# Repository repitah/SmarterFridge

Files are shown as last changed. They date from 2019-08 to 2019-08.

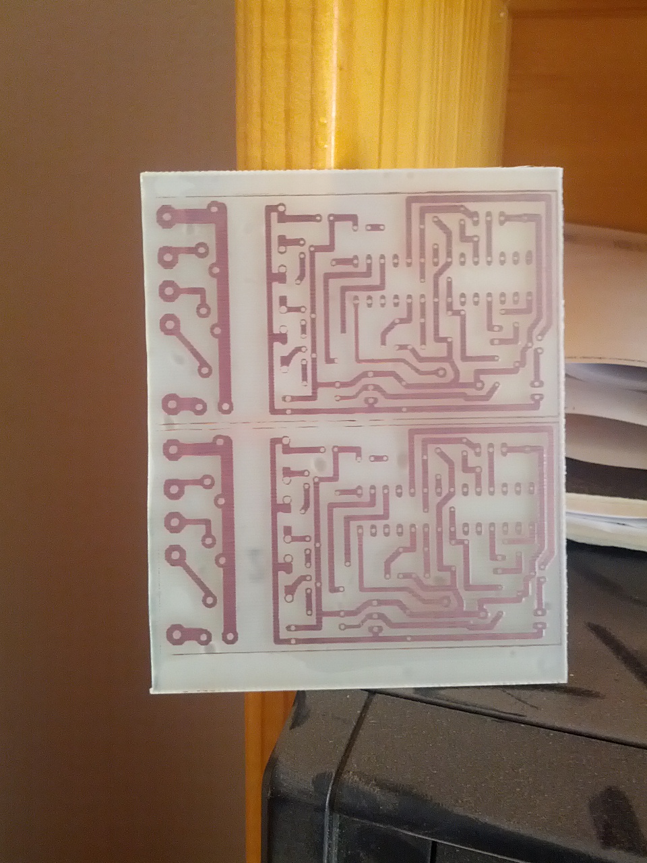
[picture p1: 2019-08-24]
Tests_misc/IMG_20130628_082345.jpg

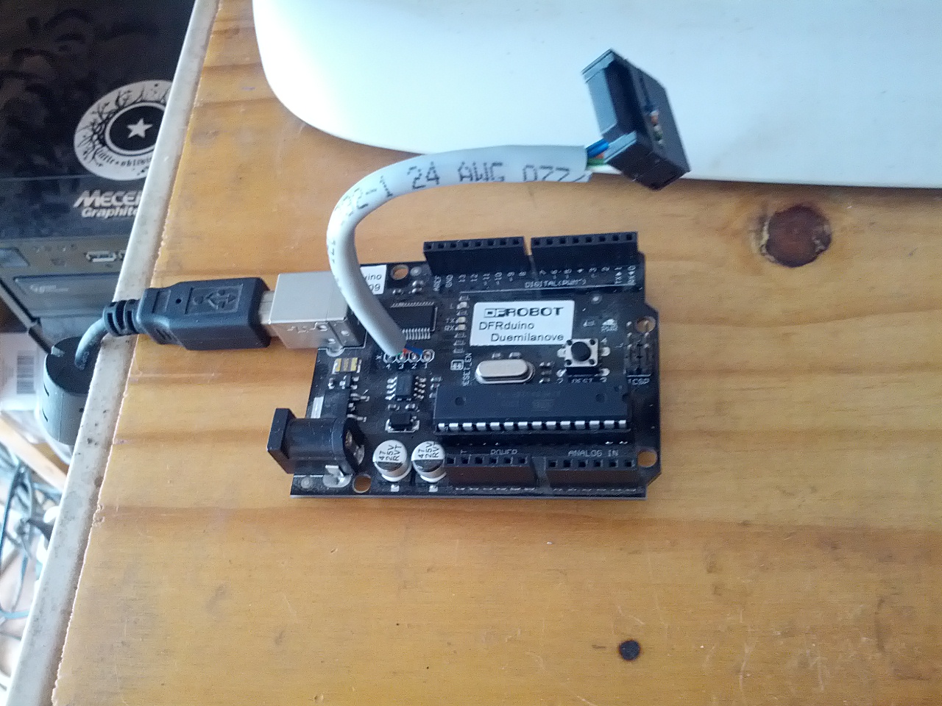
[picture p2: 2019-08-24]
Tests_misc/IMG_20130721_124718.jpg

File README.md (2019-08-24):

# SmarterFridge
Digital (AVR MCU) replacement for fridge analogue thermistat.
Circuit is essentially a custom Arduino with ATMEGA328P.

This is one of my first "major" projects (circa 2012), and a lot has been learnt since then.

Additional features (because why not)
* Fan to circulate air over the cooling radiator
  * Does not run the fan when the door is open
  * Gives an old and basic fridge more modern and expensive features.
* Door open/ajar reminder (buzzer)
* Anti-freeze / defroster (since the old fridge was a "frost-free" type.
* Does not start the compressor until the door is closed

Project notes:
* Circuit and PCB done with EagleCAD -- Only learnt basic KiCAD in a later project.
* Done with Code::Blocks (painful setup, but I wanted a half decent IDE. It should convert back to Arduno IDE fairly easily.
* In hindsight:
  * Software: not using the default Arduino bootloader may be better (doesn't pulse the pins on boot); (OptiBoot?)
  * Hardware: drive the transistors, from the MCU, via a resistor and have a pulldown
  * Hardware: There are nice modular 110V/220V mains to 12V modules that could shrink the total install package size.
  * Hardware: add simple debounce circuit to door switch. Maybe even a gated debounce.
  * Hardware: The fan turned out to be annoying in terms of humming sound. With a differnt type of fan and a custom 3D printed baffle, the idea could be promissing.
  * Hardware: Maybe port to a more modern cheap platform (ESP8266/ESP32) and/or surface mount components

Background story:
The fridge I got when I moved in to my first apartment was an old 80's/90's model that had been working reasonably well for the 5 years before this project was dreamed up. The driving reasons for this projects was: the replacement analogue thermistat was expensive; I had an interest in electronics for most of my life and had a dangerously primative knowledge of circuit (inspite of doing a few subjects in university); Arduinos were all the rage; I wanted to learn and most of the fancy fridges had some MCU type setup. Above all, the over-running of the compressor was costing me a small fortune in electricity and spoiling my fresh fruit and veg... it had to be fixed... I wanted to learn... I wasn't spending a small fortunate buying a new fridge because of 1 bad part.

My then partner, being a freshly minted professional programmer, helped me setup Code::Blocks as I wanted an IDE more akin to Visual Studio, or at least better than the basic notepad like setup that shipped for the Arduino back then (early 2010's).

The project was fun, learning about NTC resistors, voltage dividers, and even how to do lithography and make a PCB with cheap pool acid. It was also an introduction to HVAC to me -- something useful later in my career.

Sadly, 4 years later, I got home one warm summer evening and found the fridge had given up on me (I suspect a refridgerant leak, causing overheat/failure of the compressor) and was replaced with another basic fridge with analogue thermistat, the very next day -- and so this project may still be useful to necro at some point.

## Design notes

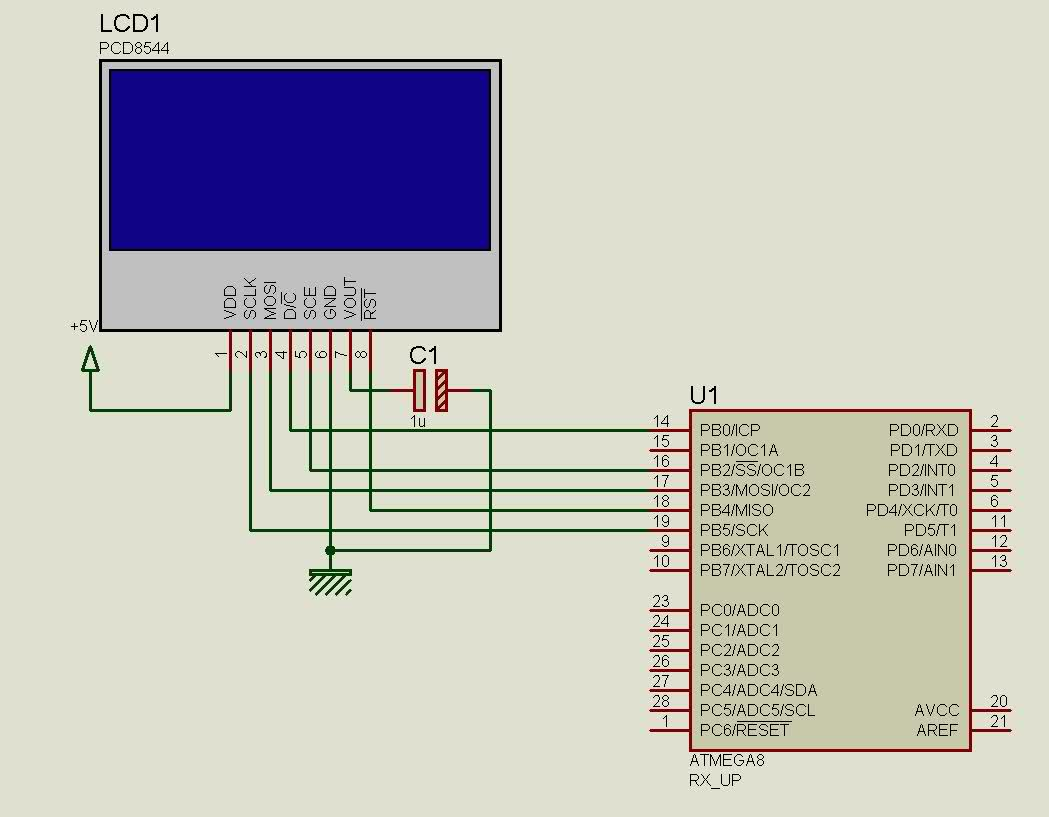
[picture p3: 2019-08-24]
Software/PCD8544/7ze9rr6f.bmp

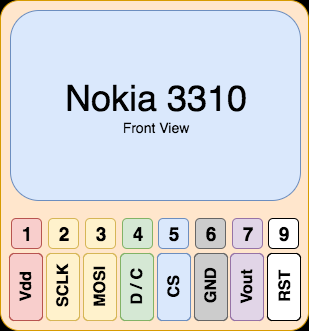
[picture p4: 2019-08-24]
Software/PCD8544/r6rif0q3.bmp

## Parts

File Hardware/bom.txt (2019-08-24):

Partlist

Exported from fridge.sch at 2013/06/12 11:44:57 AM

EAGLE Version 6.4.0 Copyright (c) 1988-2013 CadSoft

Assembly variant: 

Part        Value                Device               Package        Library       Sheet

220V-INPUT  220V-in              W237-102             W237-102       con-wago-500  1
220V-OUTPUT 220V-Outputs         W237-103             W237-103       con-wago-500  1
BUZZER                           M02                  02P            con-amp-quick 1
C1          100n                 C-EU025-025X050      C025-025X050   rcl           1
C2          22p                  C-EU025-024X044      C025-024X044   rcl           1
C3          22p                  C-EU025-024X044      C025-024X044   rcl           1
C5          100n                 C-EU025-030X050      C025-030X050   rcl           1
C6          100u                 CPOL-EUB45181A       B45181A        rcl           1
C7          100u                 CPOL-EUB45181A       B45181A        rcl           1
C9          100n                 C-EU025-050X050      C025-050X050   rcl           1
D1          1N4148DO35-7         1N4148DO35-7         DO35-7         diode         1
DOORSW                           M02                  02P            con-amp-quick 1
FAN         Fan-Connector        W237-102             W237-102       con-wago-500  1
IC1         ATMEGA8              AT90S4433P           DIL28-3        atmel         1
IC4         MC33269T-5.0         MC33269T-5.0         TO220V         linear        1
K1          V23148-A0005-A101-CO V23148-A0005-A101-CO V23148-CO      relay         1
K2          V23148-A0005-A101-CO V23148-A0005-A101-CO V23148-CO      relay         1
K3          V23148-A0005-A101-CO V23148-A0005-A101-CO V23148-CO      relay         1
PWRLED      red                  LED5MM               LED5MM         led           1
Q1          NPN_9013_SMD         TRANSISTOR-NPN-TO-92 TO-92-TRIANGLE Discrete      1
Q2          16MHz                CRYTALHC49S          HC49/S         crystal       1
Q3          NPN_9013_SMD         TRANSISTOR-NPN-TO-92 TO-92-TRIANGLE Discrete      1
Q4          NPN_9013_SMD         TRANSISTOR-NPN-TO-92 TO-92-TRIANGLE Discrete      1
Q5          NPN_9013_SMD         TRANSISTOR-NPN-TO-92 TO-92-TRIANGLE Discrete      1
R1          10k                  R-EU_0204/2V         0204V          rcl           1
R3                               R-US_0204/5          0204/5         resistor      1
R4                               R-US_0204/5          0204/5         resistor      1
R5                               R-US_0204/5          0204/5         resistor      1
R6          1k                   R-EU_0204/7          0204/7         rcl           1
R7                               R-US_0207/7          0207/7         resistor      1
R8                               R-US_0204/5          0204/5         resistor      1
SL1         DC in                M02                  02P            con-amp-quick 1
SL2         AC PSU               M02                  02P            con-amp-quick 1
TEMPSETTING                      M03                  03P            con-amp-quick 1
THERM+                           2,54/0,8             2,54/0,8       wirepad       1
THERMGND                         2,54/0,8             2,54/0,8       wirepad       1

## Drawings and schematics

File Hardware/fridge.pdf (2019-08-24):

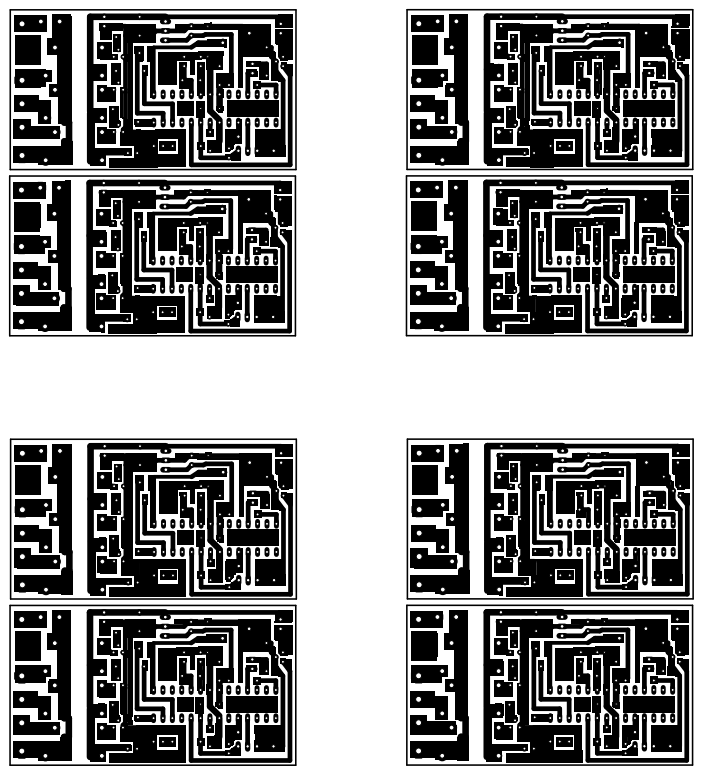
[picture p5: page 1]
GND GNDGND

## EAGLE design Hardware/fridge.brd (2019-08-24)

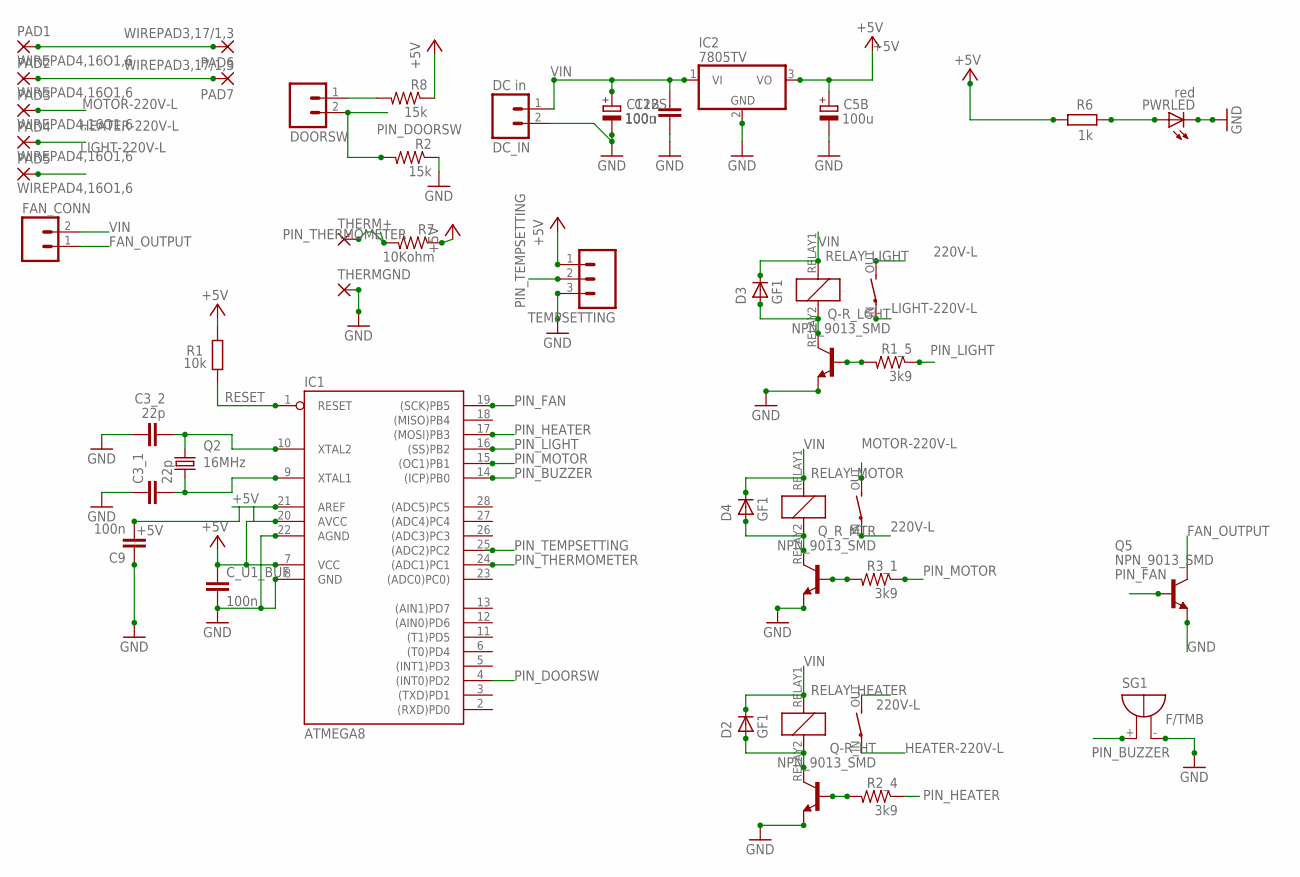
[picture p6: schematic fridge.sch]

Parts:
C3_1, C3_2: 22p; C025-025X050
C5B, C12B: 100u; E2,5-7
C9: 100n; C050-030X075
C12S: 100n; C050-035X075
C_U1_BUF: 100n; C050-035X075
D2, D3, D4: GF1; SMA-DO214AC
DC_IN: DC in; 02P
DOORSW: M02; 02P
FAN_CONN: M02; 02P
IC1: ATMEGA8; DIL28-3
IC2: 7805TV; TO220V
PAD1, PAD2, PAD3, PAD4, PAD5: WIREPAD4,16O1,6; 4,16O1,6
PAD6, PAD7: WIREPAD3,17/1,3; 3,17/1,3
PWRLED: red; LED5MM
Q2: 16MHz; HC49/S
Q5: NPN_9013_SMD; TO92
Q-R_HT: NPN_9013_SMD; TO92
Q-R_LGHT: NPN_9013_SMD; TO92
Q_R_MTR: NPN_9013_SMD; TO92
R1: 10k; 0204/7
R1_5, R2_4, R3_1: 3k9; 0204/7
R2, R8: 15k; 0204V
R6: 1k; 0204/7
R7: 10Kohm; 0204V
RELAY_HEATER: OJE-SS-112HMFSPSTOJE-SS-112HMF; OJ/OJE_SERIES
RELAY_LIGHT: OJE-SS-112HMFSPSTOJE-SS-112HMF; OJ/OJE_SERIES
RELAY_MOTOR: OJE-SS-112HMFSPSTOJE-SS-112HMF; OJ/OJE_SERIES
SG1: F/TMB
TEMPSETTING: M03; 03P
THERM+: 1,6/0,9
THERMGND: 1,6/0,9

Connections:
220V-L: PAD1.1, PAD6.1, RELAY_HEATER.OUT, RELAY_LIGHT.OUT, RELAY_MOTOR.IN
220V-N: PAD2.1, PAD7.1
+5V: C5B.+, C9.2, C_U1_BUF.1, IC1.7 (VCC), IC1.20 (AVCC), IC1.21 (AREF), IC2.3 (VO), R1.2, R6.1, R7.1, R8.1, TEMPSETTING.1
FAN_OUTPUT: FAN_CONN.1, Q5.3 (C)
GND: C3_1.1, C3_2.1, C5B.-, C9.1, C12B.-, C12S.1, C_U1_BUF.2, DC_IN.2, IC1.8 (GND), IC1.22 (AGND), IC2.2 (GND), PWRLED.K (C), Q5.1 (E), Q-R_HT.1 (E), Q-R_LGHT.1 (E), Q_R_MTR.1 (E), R2.1, SG1.-, TEMPSETTING.3, THERMGND.1
HEATER-220V-L: PAD4.1, RELAY_HEATER.IN
LIGHT-220V-L: PAD5.1, RELAY_LIGHT.IN
MOTOR-220V-L: PAD3.1, RELAY_MOTOR.OUT
unnamed: DOORSW.1, R8.2
unnamed: Q-R_HT.2 (B), R2_4.2
unnamed: PWRLED.A, R6.2
unnamed: D2.A, Q-R_HT.3 (C), RELAY_HEATER.RELAY2 (RELAY_2)
unnamed: Q-R_LGHT.2 (B), R1_5.2
unnamed: C3_1.2, IC1.9 (XTAL1), Q2.1
unnamed: C3_2.2, IC1.10 (XTAL2), Q2.2
unnamed: D4.A, Q_R_MTR.3 (C), RELAY_MOTOR.RELAY2 (RELAY_2)
unnamed: Q_R_MTR.2 (B), R3_1.2
unnamed: D3.A, Q-R_LGHT.3 (C), RELAY_LIGHT.RELAY2 (RELAY_2)
PIN_BUZZER: IC1.14 ((ICP)PB0), SG1.+
PIN_DOORSW: DOORSW.2, IC1.4 ((INT0)PD2), R2.2
PIN_FAN: IC1.19 ((SCK)PB5), Q5.2 (B)
PIN_HEATER: IC1.17 ((MOSI)PB3), R2_4.1
PIN_LIGHT: IC1.16 ((SS)PB2), R1_5.1
PIN_MOTOR: IC1.15 ((OC1)PB1), R3_1.1
PIN_TEMPSETTING: IC1.25 ((ADC2)PC2), TEMPSETTING.2
PIN_THERMOMETER: IC1.24 ((ADC1)PC1), R7.2, THERM+.1
RESET: IC1.1 (RESET), R1.1
VIN: C12B.+, C12S.2, D2.K (C), D3.K (C), D4.K (C), DC_IN.1, FAN_CONN.2, IC2.1 (VI), RELAY_HEATER.RELAY1 (RELAY_1), RELAY_LIGHT.RELAY1 (RELAY_1), RELAY_MOTOR.RELAY1 (RELAY_1)

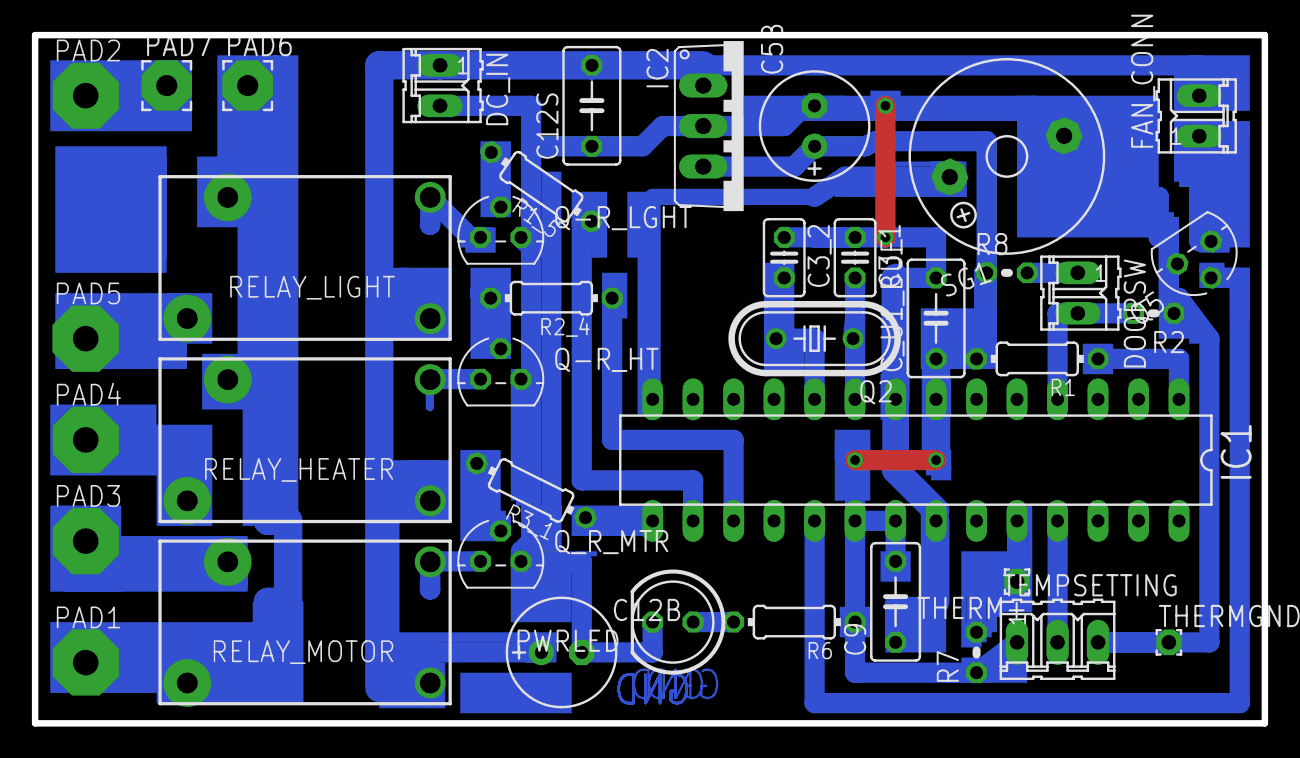
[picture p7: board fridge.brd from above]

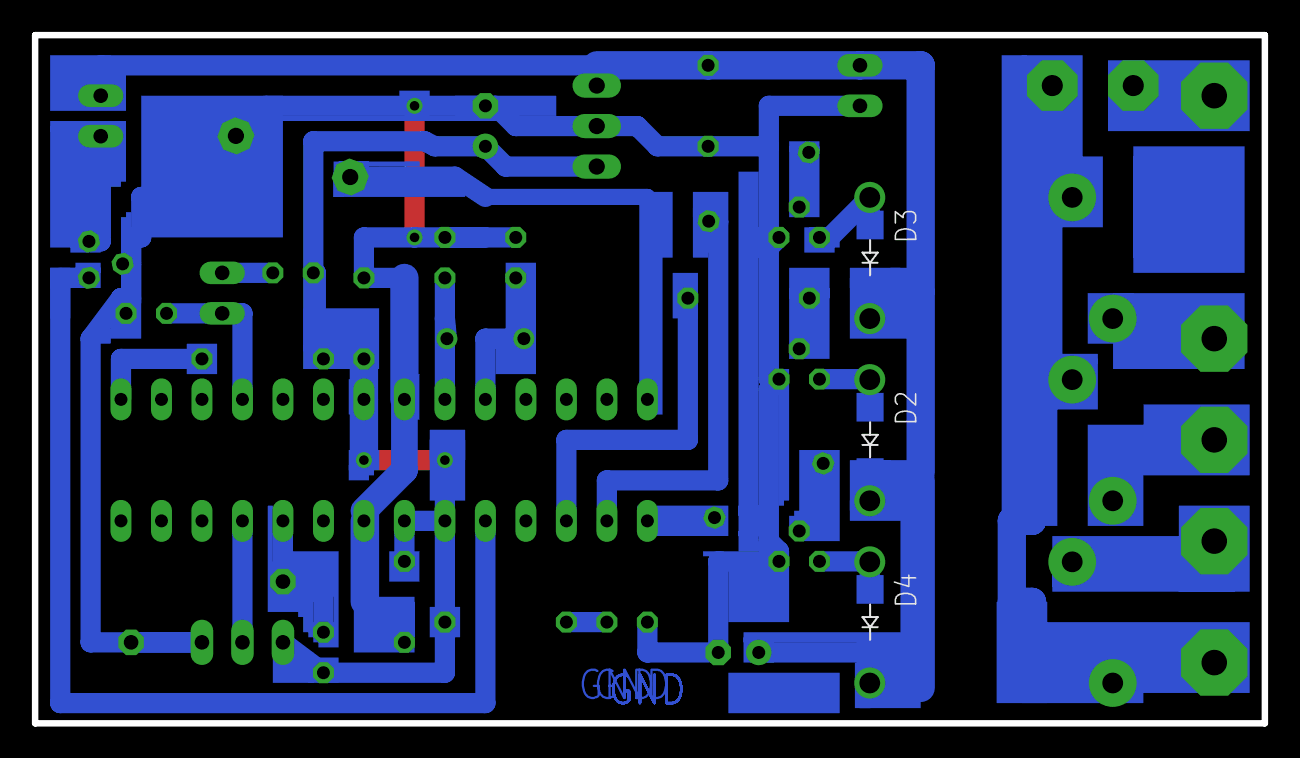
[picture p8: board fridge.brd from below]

Board: 2 copper layers, 77.1 x 43.2 mm, 43 parts (3 on the bottom side), 28 nets.

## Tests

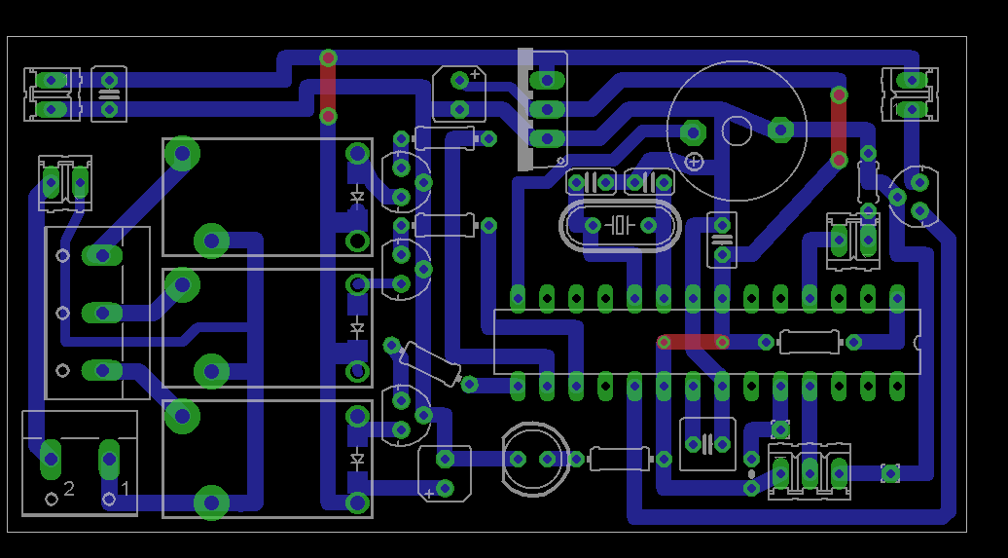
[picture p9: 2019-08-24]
Tests_misc/Layout.png

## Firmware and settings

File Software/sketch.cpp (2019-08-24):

#include <Arduino.h>
#include <string.h>
#include <avr/sleep.h>
#include <avr/power.h>
#include <avr/wdt.h>
#include <avr/interrupt.h>
#include "libraries/Thermometer/Thermometer.h"

#ifdef USELCD
#include "libraries/PCD8544/PCD8544.h"
static PCD8544 lcd (3,4,5,6,7);
#endif

//#define SERIAL_DEBUG


volatile int f_wdt=1;
//int sleepStatus = 0;             // variable to store a request for sleep

static Thermometer thermometer(A1,2000,298.15,3700); //Use pin A1 to get temperature.

const unsigned char pinDoorSW   = 2; //int0
const unsigned char pinFan      = 13;
const unsigned char pinMotor    = 9;
const unsigned char pinHeater   = 11;
const unsigned char pinLight    = 10;
const unsigned char pinBuzzer   = 8;//8;
const unsigned int buzzerfrequency = 1400;//262;

unsigned char temperature_dial = 0;
unsigned char temperature_dial_divider = 25;
float temperature_desired;
float temperature_desired_max = 10; //should be around 5 to 10 degrees
float temperature_desired_min = 4; //should be around 5 to 10 degrees
const float temperature_hysterysis = 1;

#ifdef SERIAL_DEBUG
const unsigned int heater_max_time = 40;
const unsigned int motor_min_time = 50; //3 min
const unsigned int door_open_max = 20;
#else
const unsigned int heater_max_time = 80;
const unsigned int motor_min_time = 360; //3 min
const unsigned int door_open_max = 120; //1 Minute
#endif

//bool tempbool=false;
bool state_fan=false;
bool state_door=false;
bool state_motor=false;
bool state_buzzer=false;
bool state_heater=false;
//int count = 0;                   // counter
unsigned int count_door = 0;
unsigned int cooling_state_time_since_change=0;

void setupSleep(void) {//init WDT
    MCUSR = 0x00; //clear all reset flags

    WDTCSR |= (1<<WDCE) | (1<<WDE); // In order to change WDE or the prescaler, we need to set WDCE (This will allow updates for 4 clock cycles).


    /* set new watchdog timeout prescaler value */
    //WDTCSR = 0<<WDP3 | 0<<WDP2 | 0<<WDP1 | 0<<WDP0; /* 16ms */
    //WDTCSR = 0<<WDP3 | 0<<WDP2 | 0<<WDP1 | 1<<WDP0; /* 32ms */
    //WDTCSR = 0<<WDP3 | 0<<WDP2 | 1<<WDP1 | 0<<WDP0; /* 64ms */
    //WDTCSR = 0<<WDP3 | 0<<WDP2 | 1<<WDP1 | 1<<WDP0; /* 0.125 seconds */
    //WDTCSR = 0<<WDP3 | 1<<WDP2 | 0<<WDP1 | 0<<DP0; /* 0.25 seconds */
    WDTCSR = 0<<WDP3 | 1<<WDP2 | 0<<WDP1 | 1<<WDP0; /* 0.5 seconds */
    //WDTCSR = 0<<WDP3 | 1<<WDP2 | 1<<WDP1 | 0<<WDP0; /* 1.0 seconds */
    //WDTCSR = 0<<WDP3 | 1<<WDP2 | 1<<WDP1 | 1<<WDP0; /* 2.0 seconds */
    //WDTCSR = 1<<WDP3 | 0<<WDP2 | 0<<WDP1 | 0<<WDP0; /* 4.0 seconds */
    //WDTCSR = 1<<WDP3 | 0<<WDP2 | 0<<WDP1 | 1<<WDP0; /* 8.0 seconds */

    WDTCSR |= (1<<WDIE);//enable watchdog interrupt

    #ifdef SERIAL_DEBUG
        set_sleep_mode(SLEEP_MODE_IDLE);     // sleep mode is set here Power Down uses the least current
    #else
        set_sleep_mode(SLEEP_MODE_PWR_DOWN);     // sleep mode is set here Power Down uses the least current
    #endif
}

ISR(WDT_vect){ //Runs whenever the sleep timer is reached
}

void enterSleep(void){
    sleep_enable();
    sleep_mode();

    /* The program will continue from here after the WDT timeout*/
    sleep_disable(); /* First thing to do is disable sleep. */

    //power_all_enable();
    //power_adc_enable();
}

void buzzer(){
        #ifdef SERIAL_DEBUG
            Serial.println("Buzzer()");
        #endif
        tone(pinBuzzer,buzzerfrequency,1000/4);
        #ifndef SERIAL_DEBUG
        delay(1000/4);
        noTone(pinBuzzer);
        #endif
        //tone(pinBuzzer,buzzerfrequency,1000/4);
        //delay(1000/4);

}

void updateOutputs(){ //change the states of the heater, fan and motor
    noInterrupts(); //prevent relays causing a door trigger
    digitalWrite(pinLight, state_door);
    digitalWrite(pinMotor,state_motor);
    digitalWrite(pinFan,state_fan);
    digitalWrite(pinHeater,state_heater);
    delay(75); //allow time for relay to activate
    interrupts(); //reenable interrupts
}

#ifdef USELCD
void lcdupdate(){
    String displaystr;

    //lcd.clear();
    lcd.setCursor(0, 0); lcd.clearLine();
    lcd.print("Temp: ");
    lcd.print(thermometer.temperature ,2);
    lcd.println("'C");

    lcd.setCursor(0, 1);lcd.clearLine();

    if (state_fan) lcd.print("FAN: ON"); else lcd.print("FAN: OFF");

    lcd.setCursor(0, 2);lcd.clearLine();
    if (state_motor) lcd.print("Motor: ON"); else lcd.print("Motor: OFF");

    lcd.setCursor(0, 3);lcd.clearLine();
    if (state_heater) lcd.print("Heater: ON"); else lcd.print("Heater: OFF");

    lcd.setCursor(0, 4);lcd.clearLine();
    //lcd.print("Count_door: "); lcd.print(count_door);
    lcd.print("TempD: "); lcd.print(temperature_desired);

    lcd.setCursor(0, 5);lcd.clearLine();
    lcd.print("Sttng: "); lcd.print(temperature_dial);
 //   lcd.print("Cool#: "); lcd.print(cooling_state_time_since_change);
}
#endif

void doorTrigger(){
    detachInterrupt(0);
    sei();
    delay(50);
    state_door=digitalRead(pinDoorSW);
    if (state_door){ //switch off fan immediately on door open
            state_fan = false;
    } else if (state_motor){ //switch on fan immediately on door close and motor running
        state_fan = true;
    };
    count_door=0; //reset door counter to zero on every door action
    updateOutputs();

    #ifdef SERIAL_DEBUG
    Serial.println();
    Serial.println("**************************************************");
    Serial.print("DOOR STATE CHANGED "); Serial.println(state_door);
    Serial.println("**************************************************");
    #endif
    delay(200);
    attachInterrupt(0,doorTrigger,CHANGE);
}

void setup(){

    EIMSK != _BV(INT0);
    sei();

    analogReference(DEFAULT);

    #ifdef SERIAL_DEBUG
        pinMode(2, OUTPUT);
        Serial.begin(9600);
        delay(1000);
        Serial.println("Executing Setup()");
        delay(2000);
    #endif
    #ifdef USELCD
        lcd.begin(84, 48);
    #endif

    setupSleep();

    /*Check these
    power_spi_disable();
    power_timer1_disable(); //Timer 0 will also stop WDT, which I need
    power_timer2_disable();
    */

    power_twi_disable();

    //Setup pins
    delay(10);
    pinMode(pinDoorSW,INPUT);
    pinMode(pinLight,OUTPUT);
    pinMode(pinMotor,OUTPUT);
    pinMode(pinHeater,OUTPUT);
    pinMode(pinFan,OUTPUT);

    doorTrigger(); //read the door state on power on
    thermometer.update();



}

void heater(bool enabled){
    static bool active_state; //False = off; True = on with tomer
    static unsigned int timer;
    if (enabled && (thermometer.temperature >= temperature_desired) && (timer > (heater_max_time / 2))) enabled = false;

    if (enabled && active_state==false){
        timer = 0;
        state_heater = true;
        active_state = true;
    }
    if (enabled && active_state==true){
        if (timer > heater_max_time) {
            state_heater = false;
        } else {
            timer++;
        }
    }
    if (!enabled){
        state_heater = false;
        active_state = false;
    }
}

void setCoolingState(){
    static bool active_state; //False = warming, True = cooling

    if  (temperature_dial == (1024 /  temperature_dial_divider)){ //if dial @ 0
        //tone(pinBuzzer,buzzerfrequency,1000/4);
        state_fan = false;
        state_motor = false;
        heater(false);
        cooling_state_time_since_change=0;
    } else {
        temperature_desired = temperature_desired_max - temperature_desired_min;
        temperature_desired = temperature_desired * (float (temperature_dial) / (1024  / temperature_dial_divider));
        temperature_desired = temperature_desired_min + temperature_desired;
        if ((cooling_state_time_since_change > 0) && (cooling_state_time_since_change < (motor_min_time + 1))) { //deny change of state, unless time=0=just turned on
            cooling_state_time_since_change++;
        } else { //Allow the change of state
            if (!state_door && (thermometer.temperature > ( temperature_desired + (temperature_hysterysis / 2)))) { //Switch on cooling
                if (!active_state){
                    active_state = true;
                    cooling_state_time_since_change = 1;
                }
            }
            if (thermometer.temperature < ( temperature_desired - (temperature_hysterysis / 2))) { //Switch off cooling
                if (active_state){
                    active_state = false;
                    cooling_state_time_since_change = 1;
                }
            }
        }
        switch (active_state){
        case true :
            if (!state_door) {state_fan = true;}
            state_motor = true;
            heater(false);
            break;
        case false:
            state_fan = false;
            state_motor = false;
            heater(true);
        }
    }
}

void doorState(){
    #ifdef USELCD
    lcd.setPower(state_door);
    #endif
    if (state_door){ //Door open
        if (count_door < door_open_max) {
            count_door++;
        } else {
            state_buzzer = true;
        }
    } else { //Door closed
        state_buzzer=false; //always make it false
        switch (count_door){
            case 6:
                #ifdef USELCD
                lcd.setPower(false);
                #endif
                count_door++;
                break;
            case 65530 :
                count_door = 7;
                break;
            default:
                count_door++;
        }
    }

    if (state_buzzer) buzzer();
}

void loop(){
    f_wdt=0;

    state_door=digitalRead(pinDoorSW);
    doorState();
    temperature_dial = round(analogRead(A2) / temperature_dial_divider);
    thermometer.update();
    setCoolingState();
    updateOutputs();

    #ifdef USELCD
    lcdupdate();
    #endif

    #ifdef SERIAL_DEBUG
    Serial.write("\r\n\r\n\r\n");
    Serial.print("Tempterature dial: "); Serial.println(temperature_dial);
    Serial.print("Temperature desired: ");Serial.println(temperature_desired);
    Serial.print("Temperature: ");Serial.println(thermometer.temperature);
    Serial.print("   State Door: "); Serial.println(state_door);
    Serial.print(" State Buzzer: "); Serial.println(state_buzzer);
    Serial.print("  State Motor: "); Serial.println(state_motor);
    Serial.print(" State Heater: "); Serial.println(state_heater);
    Serial.print(    "State Fan: "); Serial.println(state_fan);
    Serial.print("   Door count: "); Serial.println(count_door);
    Serial.print("Time since change : ");Serial.println(cooling_state_time_since_change);
    Serial.print("Digital pin 2 value:"); Serial.println(digitalRead(pinDoorSW));
    delay(500);
    #endif

    enterSleep();
}

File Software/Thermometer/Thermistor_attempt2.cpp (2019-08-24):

#include <avr/sleep.h>
#include <avr/power.h>
#include <avr/wdt.h>

volatile int f_wdt=1;
boolean led_state=false;

word Analog0 = 0;    // first analog sensor
short temp = 0;   // second analog sensor

/*
Thermistor Specifications:
T0 = 25^C
R0 = 1000 ohm
K  = 3700

Voltage divider Specifications:
Vin = 5V
 |
 R = 10k
 +- Vout
 |
Thermistor = 1000 @ 25 / B=3700
 |
GND
*/
double Rinf;

int sleepStatus = 0;             // variable to store a request for sleep
int count = 0;                   // counter
  
void setup()
{
  // start serial port at 9600 bps:
  Serial.begin(9600);
  Rinf = 1000 * exp(-3700 / 298.15); //R0 * exp(-B / T0)
  
  
  pinMode(2, OUTPUT);
  setupSleep();
  power_spi_disable();
  power_timer1_disable(); //Timer 0 will also stop WDT, which I need
  power_timer2_disable();
  power_twi_disable();
}

void loop()
{ 
  f_wdt=0;
  //Serial.println("About to sleep");
  enterSleep();
  //Serial.println("Awake");
  led_state = !led_state;
  digitalWrite(13, led_state);
  Serial.println(tempC());
  //delay(300);
}

float tempC()
{
  long Rval = 0;
  for (byte count = 0; count < 32; count++){ //get an average reading of Vout
    Rval += analogRead(A0);
  }
  Rval /= 32;
  Rval = (Rval * 10000) / (1023 - Rval); //Convert average Vout to Rtherm

  return 3700 / log(Rval / Rinf) - 273.15; //Convert Rtherm to temperature in degrees centigrade.
}

ISR(WDT_vect)
{
  if(f_wdt == 0)
  {
    f_wdt=1;
  }
  else
  {
    Serial.println("WDT Overrun!!!");
  }
}

void enterSleep(void)
{
  set_sleep_mode(SLEEP_MODE_PWR_SAVE);
  
  sleep_enable();
  power_usart0_disable();
  sleep_mode();
  
  /* The program will continue from here after the WDT timeout*/
  power_usart0_enable();
  delay(10);
  Serial.println();
  //Serial.println("Continuing");
  sleep_disable(); /* First thing to do is disable sleep. */
  
  //power_all_enable();
  //power_adc_enable();
}

void setupSleep(void) //init WDT
{
  // Clear the reset flag.
  MCUSR &= ~(1<<WDRF);
  
  // In order to change WDE or the prescaler, we need to set WDCE (This will allow updates for 4 clock cycles).
  WDTCSR |= (1<<WDCE) | (1<<WDE);

  // set new watchdog timeout prescaler value
  //WDTCSR = 0<<WDP3 | 0<<WDP2 | 0<<WDP1 | 0<<WDP0; /* 16ms */
  //WDTCSR = 0<<WDP3 | 0<<WDP2 | 0<<WDP1 | 1<<WDP0; /* 32ms */
  //WDTCSR = 0<<WDP3 | 0<<WDP2 | 1<<WDP1 | 0<<WDP0; /* 64ms */
  //WDTCSR = 0<<WDP3 | 0<<WDP2 | 1<<WDP1 | 1<<WDP0; /* 0.125 seconds */
  //WDTCSR = 0<<WDP3 | 1<<WDP2 | 0<<WDP1 | 0<<DP0; /* 0.25 seconds */
  //WDTCSR = 0<<WDP3 | 1<<WDP2 | 0<<WDP1 | 1<<WDP0; /* 0.5 seconds */
  WDTCSR = 0<<WDP3 | 1<<WDP2 | 1<<WDP1 | 0<<WDP0; /* 1.0 seconds */
  //WDTCSR = 0<<WDP3 | 1<<WDP2 | 1<<WDP1 | 1<<WDP0; /* 2.0 seconds */
  //WDTCSR = 1<<WDP3 | 0<<WDP2 | 0<<WDP1 | 0<<WDP0; /* 4.0 seconds */
  //WDTCSR = 1<<WDP3 | 0<<WDP2 | 0<<WDP1 | 1<<WDP0; /* 8.0 seconds */
  
  /* Enable the WD interrupt (note no reset). */
  WDTCSR |= _BV(WDIE);
}

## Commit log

2019-08-24 Initial hardware dump
    [fridge.brd, fridge.sch]
2019-08-24 Original PCB Layout
